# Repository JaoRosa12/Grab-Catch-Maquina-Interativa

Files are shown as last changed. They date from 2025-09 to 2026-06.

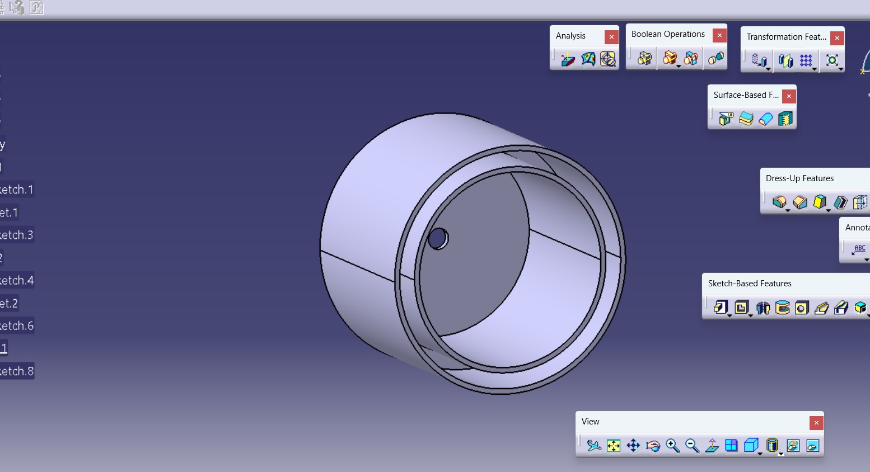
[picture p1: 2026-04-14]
DIP 06/2° Sprint/modelo 3D.jpeg

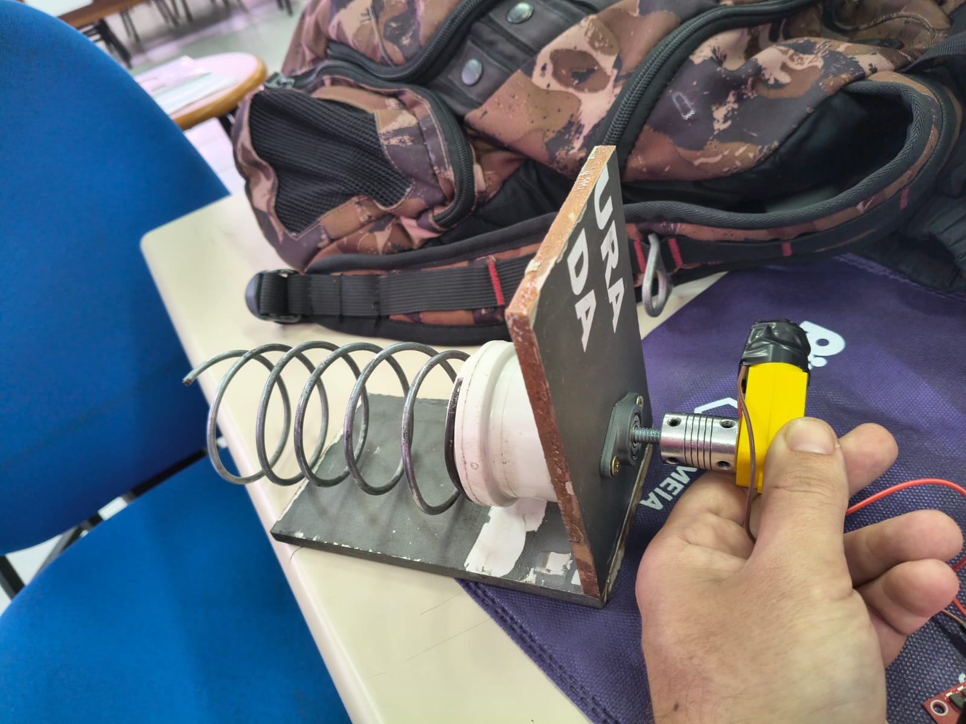
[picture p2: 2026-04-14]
DIP 06/2° Sprint/simulação mola 2.jpeg

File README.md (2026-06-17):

# Organizações Grab & Catch - Maquina Interativa

## 📌 Introdução

A Grab & Catch é uma máquina interativa desenvolvida por alunos do curso de Manufatura Avançada da Fatec São José dos Campos, no âmbito da disciplina de Desenvolvimento Integrado de Produto (DIP). A proposta é simples: o usuário enfrenta um jogo rápido na tela TFT Touch, e se vencer, ganha um brinde liberado na hora pela máquina.

O projeto integra sistemas mecânicos, eletrônicos e de programação em um único protótipo funcional, demonstrando na prática a relação entre hardware e software no processo de automação. O painel de controle é simples e acessível, com uma interface intuitiva que facilita a interação do usuário com a máquina.

## 🎯 Objetivos	

Este projeto tem como finalidade desenvolver uma máquina interativa, que proporcione praticidade e interatividade aos usuários. Para isso, será implementado um sistema de pontos e caso o usuário consiga ganhar determinados pontos, poderá escolher algum produto da máquina.

Além disso, a máquina terá um design interno que facilite tanto o armazenamento quanto a reposição contínua dos produtos. Serão também definidas normas operacionais que assegurem o uso seguro e a manutenção adequada do equipamento.

O desenvolvimento será dividido em etapas específicas, nas quais cada módulo do sistema será projetado e testado individualmente antes da integração final. A equipe contará com o apoio de orientadores para alinhar as funcionalidades às necessidades reais, promovendo ajustes contínuos ao longo do processo. O andamento será acompanhado por meio de um cronograma estruturado, que organizará as entregas e facilitará o monitoramento das atividades.

## Cronograma Macro - Entrega até a Feira de Soluções

#### Entrega 1 

| Tarefas | Colaborador | Início | Fim | 
|---|---|---|-----|
| ✅ Formalização das Equipes| João Pedro | 25/02/2026 | 25/02/2026 |
| ✅ Pesquisa dos Materias para Fabricação | João Vitor & Gabriel | 28/02/2026 | 10/03/2026 |
| ✅ Pesquisa sobre LCD TFT| João Pedro & Gabriel  |28/03/2026 | 04/03/2026 |
| ✅ Pesquisa sobre Micontroladores| João Pedro & Gabriel | 28/03/2026 | 03/03/2026 |
| ✅ Pesquisa sobre integração de iluminação da Maquina| Gabriel | 03/03/2026 | 11/03/2026 |
| ✅ Pré-Projeto Finalizado | João Vitor  | 08/03/2026 | 10/03/2026 |
| ✅ Documentação e Apresentação | Equipe | 12/03/2026 | 12/03/2026 |

#### Entrega 2

| Tarefas | Colaborador | Início | Fim | 
|---|---|---|-----|
| ✅ Pesquisa sobre a parte mecanica da mola| João Vitor & Gabriel | 15/03/2026 | 20/03/2026 |
| ✅ Pesquisa sobre a progrmação do LCD TFT| João Pedro | 16/03/2026 | 20/03/2026 |
| ✅ Desenvolvimento do Desenho Tecnico Atualizado| João Vitor | 18/03/2026| 08/04/2026 |
| ✅ Minuta do Projeto Finalizado | João Pedro | 26/03/2026 | 26/03/2026 |
| ✅ Documentação e Apresentação | Equipe | 09/04/2026 | 09/04/2026 |

#### Entrega 3

| Tarefas | Colaborador | Início | Fim | 
|---|---|---|-----|
| ✅ Montagem da Estrutura da Maquina| Equipe | 13/04/2026  |  04/05/2026  |
| ✅ Programar jogos para a Maquina | João Pedro |  15/04/2026  |  22/04/2026  |
| ✅ Visualização e testes de programação | João Pedro |  22/04/2026 |  22/04/2026  |
| ✅ Finalização do Projeto Executivo | João Pedro |  25/04/2026  | 25/04/2026  |
| ✅ Documentação e Apresentação | Equipe | 05/05/2026  | 06/05/2026  |

#### Entrega 4 

| Tarefas | Colaborador | Início | Fim | 
|---|---|---|-----|
| ✅ Montagem dos Eletrônicos  | Equipe |  09/05/2026  |  15/05/2026  |
| ✅ Sistema Mecânico na Estrutura | João Pedro |  09/05/2026  | 15/05/2026  |
| ✅ Teste de Validação | Equipe |  10/05/2026  |  16/05/2026  |  
| ✅ Ajustes Tecnicos  | Equipe  |  16/05/2026  | 18/05/2026 |
| ✅ Documentação e Apresentação | Equipe |  09/06/2026  |  11/06/2026 |

## 👥 Equipe Grab & Catch

O projeto é desenvolvido pelos seguintes integrantes:

| Nome | Foto | Área |
|---|---|---|
| **Gabriel Alves**, 📧 [Email](mailto:gabriel_alvesempresarial@hotmail.com) | Gabriel Alves | **Mecânica/Eletrônica**  |  
| **João Pedro da Silva Rosa**, 📧 [Email](mailto:joao.silvarosa16@gmail.com) | João Pedro Da Silva Rosa | **Programação/Eletrônica**  |
| **João Vitor Morais Souza**, 📧 [Email](mailto:joao.souza234@fatec.sp.gov.br) | João Vitor Morais Souza | **Mecânica/Eletrônica**  |

**Professores orientadores:**
- **Viviane Siqueira**

## 🔗 Links Úteis

- 🔗 Repositório no GitHub: [Organizações Grab & Catch - Maquina de Vendas](https://github.com/JaoRosa12/Grab-Catch-Maquina-de-Vendas)
- 🎥 Demonstração do Projeto: (*Adicionaremos o link para vídeos, se houver*)

## 📞 Contato

Caso tenha dúvidas ou sugestões, entre em contato com a equipe pelo GitHub ou através dos professores orientadores.

---

📌 **Organizações Grab & Catch - Maquina de Vendas** | Curso Superior de Tecnologia em Manufatura Avançada - Fatec - SJC

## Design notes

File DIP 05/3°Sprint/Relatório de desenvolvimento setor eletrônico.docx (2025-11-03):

Relatório de desenvolvimento setor eletrônico

Nesta etapa fizemos os testes em bancada dos componentes eletrônicos, ligando cada um deles em conjunto com o objetivo de validar seu funcionamento

Dividimos em 2 partes os testes em bancada sendo o primeiro com relação aos componentes de interação com o usuário

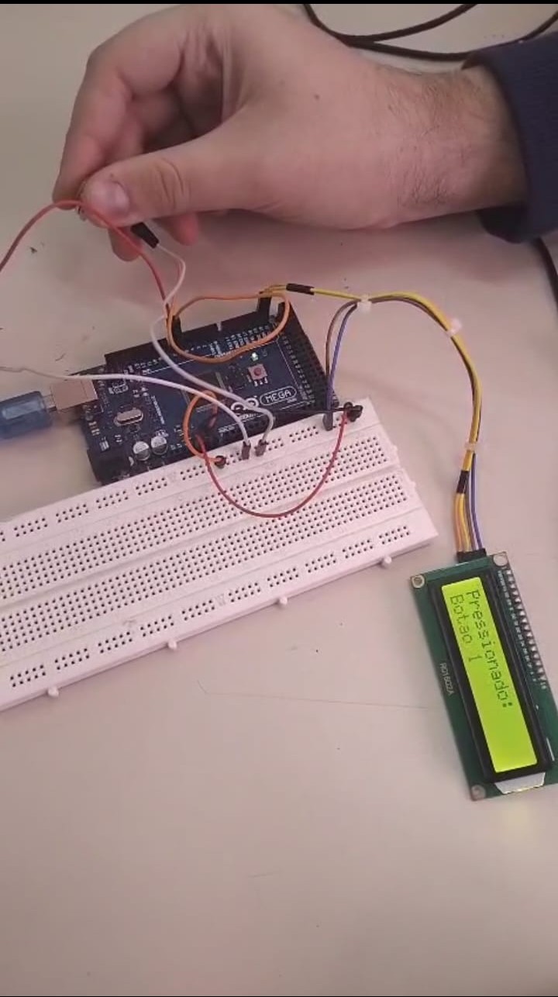
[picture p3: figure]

Componentes de teste:

- Arduino MEGA
- Display Lcd com módulo i2C
- 2 botões pushbottom

Tensão necessária para os componentes: 5V – fornecido pelo próprio Arduino

A segunda parte dos testes em bancada dessa vez foi relacionada aos componentes que irão de fato movimentar os produtos internos

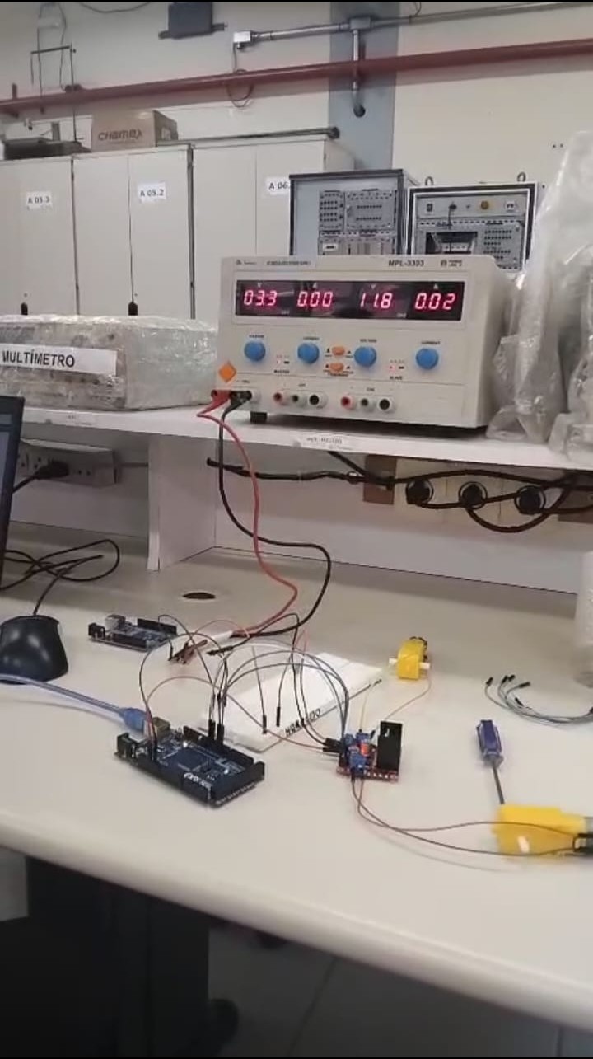
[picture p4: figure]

Componentes utilizados:

- Arduino MEGA
- Ponte H L298N
- 2 motores Dc com caixa redutora

Fonte de energia de bancada de 6V para alimentação dos motores

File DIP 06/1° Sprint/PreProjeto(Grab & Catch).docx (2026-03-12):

Curso Superior de Tecnologia em

Manufatura Avançada

projeto executivo de desenvolvimento integrado de produto VI - MÁQUINA INTERATIVA

JOÃO PEDRO DA SILVA ROSA

JOÃO VITOR MORAES DE SOUZA

GABRIEL ALVES DA SILVA

São José dos Campos

2026

RESUMO

Este pré-projeto apresenta a continuação do desenvolvimento da Máquina Interativa Grab & Catch, criada para promover a FATEC em eventos por meio de jogos interativos e distribuição de brindes. A primeira versão foi apresentada na Feira de Soluções como prova de conceito, porém apresentou limitações estruturais e mecânicas. Assim, este trabalho propõe melhorias no design, na estrutura e no sistema de funcionamento da máquina, visando tornar o protótipo mais robusto, funcional e adequado para uso em eventos institucionais.

# 1. INTRODUÇÃO

No semestre passado foi desenvolvido um projeto de uma máquina interativa que distribuía brindes para quem interagisse com seus jogos, cujo objetivo era atrair visitantes em eventos acadêmicos por meio de jogos rápidos e interativos, oferecendo brindes como recompensa pela participação do usuário. A máquina foi apresentada na Feira de Soluções da FATEC, funcionando como uma prova de conceito de um sistema interativo capaz de promover a instituição e gerar engajamento com o público.

Apesar de o projeto ter sido funcional e ter atingido seu objetivo de demonstrar o conceito da máquina interativa, alguns problemas foram observados durante o desenvolvimento e apresentação do protótipo. A estrutura construída em papel panamá apresentou baixa resistência mecânica, e o sistema de mola utilizado para a liberação dos brindes demonstrou dificuldades de funcionamento, exigindo diversos ajustes durante os testes.

Dessa forma, o presente projeto tem como proposta dar continuidade ao desenvolvimento da máquina interativa, aplicando melhorias estruturais, mecânicas e eletrônicas com base nas dificuldades identificadas no semestre anterior. A nova etapa busca tornar o protótipo mais robusto, confiável e adequado para utilização em eventos institucionais.

# 2. Justificativa

Projetos interativos são ferramentas importantes para promover instituições em eventos acadêmicos, feiras tecnológicas e atividades de divulgação científica. A utilização de sistemas automatizados capazes de oferecer experiências lúdicas ao público contribui para aumentar o interesse dos visitantes e fortalecer a imagem institucional.

Além disso, a continuação do projeto permite que os alunos aprofundem conhecimentos práticos em áreas importantes da Manufatura Avançada, como:

- Sistemas embarcados
- Integração entre eletrônica e mecânica
- Prototipagem de produtos
- Automação
- Desenvolvimento de interfaces interativas

Outro fator relevante é que o protótipo desenvolvido anteriormente apresentou limitações estruturais e mecânicas que podem ser significativamente aprimoradas nesta nova etapa do projeto. Dessa forma, a evolução da solução permitirá desenvolver um protótipo mais robusto, funcional e confiável, aproximando o projeto de um produto real.

# 3. Objetivos geral e específicos

Objetivo geral

Dar continuidade ao desenvolvimento da Máquina Interativa Grab & Catch, aplicando melhorias estruturais, mecânicas e eletrônicas para tornar o sistema mais robusto, funcional e adequado para utilização em eventos institucionais.

Objetivos específicos

Para atingir o objetivo geral deste projeto, foram definidos os seguintes objetivos específicos:

- Analisar os problemas observados no protótipo desenvolvido no semestre anterior;
- Redesenhar a estrutura física da máquina para aumentar sua resistência e estabilidade;
- Melhorar o sistema mecânico da mola responsável pela liberação dos brindes;
- Reorganizar e otimizar o sistema eletrônico baseado em Arduino;
- Substituir display LCD por um TFT Touch colorido
- Refinar o software responsável pela interface e pelos jogos interativos;

# 4. Proposta de design e funcionalidade da solução

A proposta deste projeto consiste em desenvolver uma versão aprimorada da máquina interativa Grab & Catch, mantendo o conceito original, porém com melhorias estruturais e funcionais baseadas nas dificuldades observadas anteriormente.

Estrutura desenvolvida no catia no semestre passado.

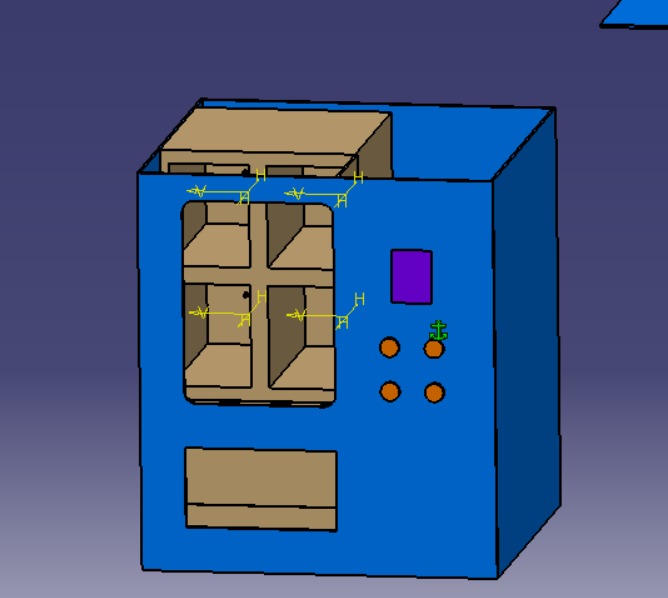
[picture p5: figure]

Fonte: Autor próprio.

Estrutura apresentada na feira de soluções no semestre passado.

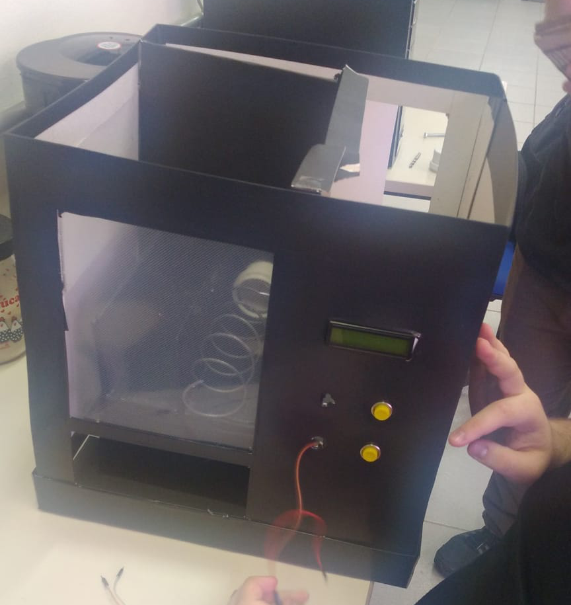
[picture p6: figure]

Fonte: Autor próprio.

# 5. Mapa Mental

Mapa mental desenvolvido.

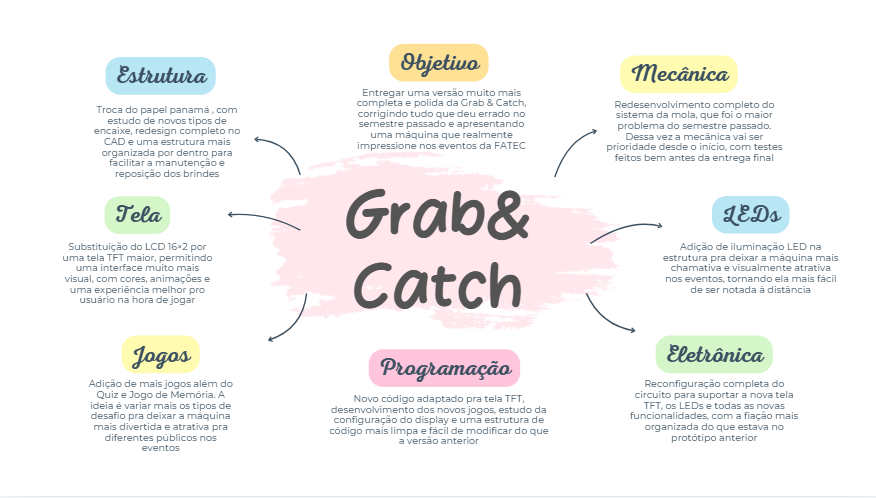
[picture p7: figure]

Fonte: Autor próprio

# 6. Lista de componentes.

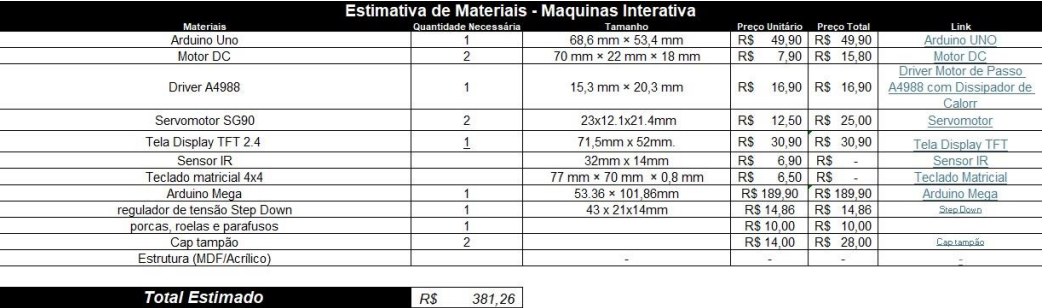
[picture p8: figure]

# 7. Cronograma Micro

Cronograma Macro desenvolvida para 1° Sprint.

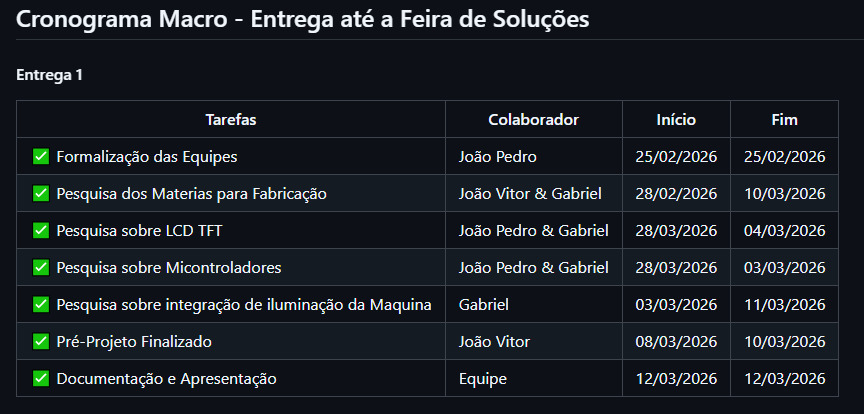
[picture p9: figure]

Fonte: Autor próprio.

# 8. REFERÊNCIAS

ARDUINO. Arduino Uno Rev3. Arduino Official Documentation, 2024. Disponível em: https://www.arduino.cc/en/Main/ArduinoBoardUno.

ARDUINO. Arduino Mega 2560 Rev3. Arduino Official Documentation, 2024. Disponível em: https://www.arduino.cc/en/Main/ArduinoBoardMega2560. Acesso em: 20 nov. 2024.

ARDUINO. LiquidCrystal Library Reference. Arduino Official Documentation, 2024. Disponível em: https://www.arduino.cc/en/Reference/LiquidCrystal

ATMEL. ATmega328P Datasheet. Atmel Corporation, 2015. Disponível em: http://www.atmel.com.

BANZI, Massimo; SHILOH, Michael. Primeiros passos com o Arduino. 2. ed. São Paulo: Novatec, 2015.

INSTRUCTABLES. Otto DIY - Build You Own Robot in Two Hours. Disponível em: https://www.instructables.com/Otto-Build-You-Own-Robot-in-Two-Hours/.

MARGOLIS, Michael. Arduino cookbook. 3. ed. Sebastopol: O'Reilly Media, 2020.

MCROBERTS, Michael. Arduino básico. São Paulo: Novatec, 2011.

MONK, Simon. Programação com Arduino: começando com sketches. 2. ed. Porto Alegre: Bookman, 2017.

TEXAS INSTRUMENTS. L293D Quadruple Half-H Driver Datasheet. Texas Instruments, 2016. Disponível em: http://www.ti.com.

Material didático do Curso Superior de Tecnologia em Manufatura Avançada. FATEC São José dos Campos, 2023-2024.

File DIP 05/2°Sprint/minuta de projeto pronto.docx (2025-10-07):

CURSO SUPERIOR DE TECNOLOGIA EM

MANUFATURA AVANÇADA

MINUTA DE PROJETO DE DESENVOLVIMENTO INTEGRADO DE PRODUTO V – MAQUINA INTERATIVA

João Pedro da Silva Rosa

João Vitor Moraes de Sousa

Gabriel Alves da Silva

# Escopo do projeto

O projeto consiste no desenvolvimento de uma máquina interativa, com o objetivo de promover a instituição FATEC. A interação presenteará aqueles que interagirem com brindes relacionados e instituição, que podem ser chaveiros, canetas, adesivos, pirulitos, bala etc. O projeto será subdividido em 3 partes principais de desenvolvimento, sendo:

- Eletrônica
- Programação
- Estrutural

O processo de desenvolvimento tem início com a montagem do circuito eletrônico do produto, que inicialmente contará com os componentes básicos para sua operação sendo:

- 2x Arduino Uno;

- 4x Motores Dc;

- 2x Driver Ponte H L298N;

- 1 Tela Display TFT 2.4 driver HX8347-D;

A partir destes componentes básicos será desenvolvido os cálculos necessários para o desenvolvimento do circuito eletrônico, relativo a suas tensões, corrente e resistências necessárias para sua aplicação

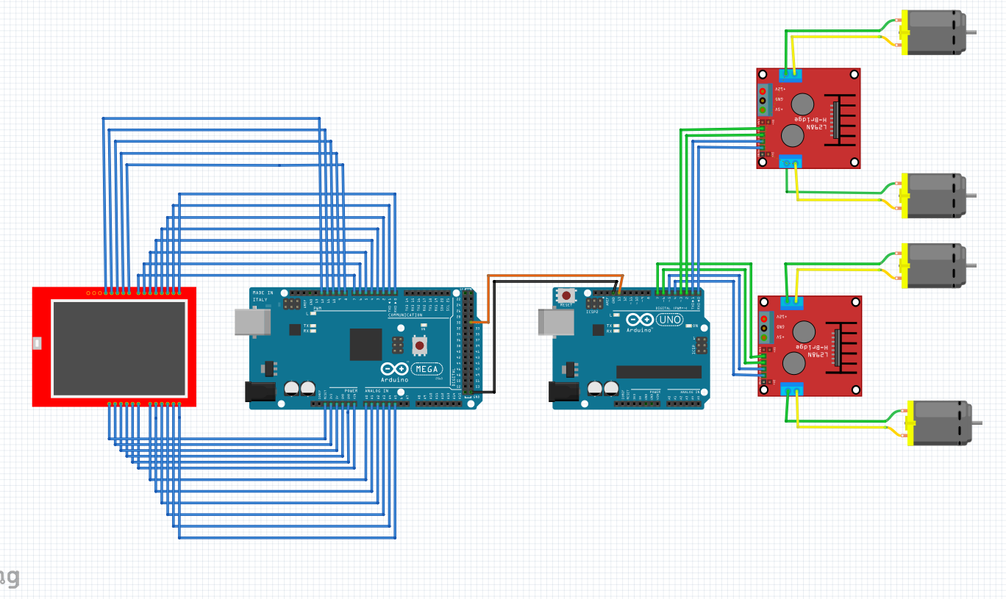
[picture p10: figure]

Fonte: autor próprio

O objetivo deste circuito primordialmente é ter uma interface de interação com o usuário (LCD) da qual com a interação do cliente se enviara um Input para os motores Dc que estarão internamente no produto, fazendo com que se acione alguma alavanca que “derrubará” o brinde ao usuário, sua recompensa pela interação.

Abaixo algumas imagens da internet retiradas como inspiração

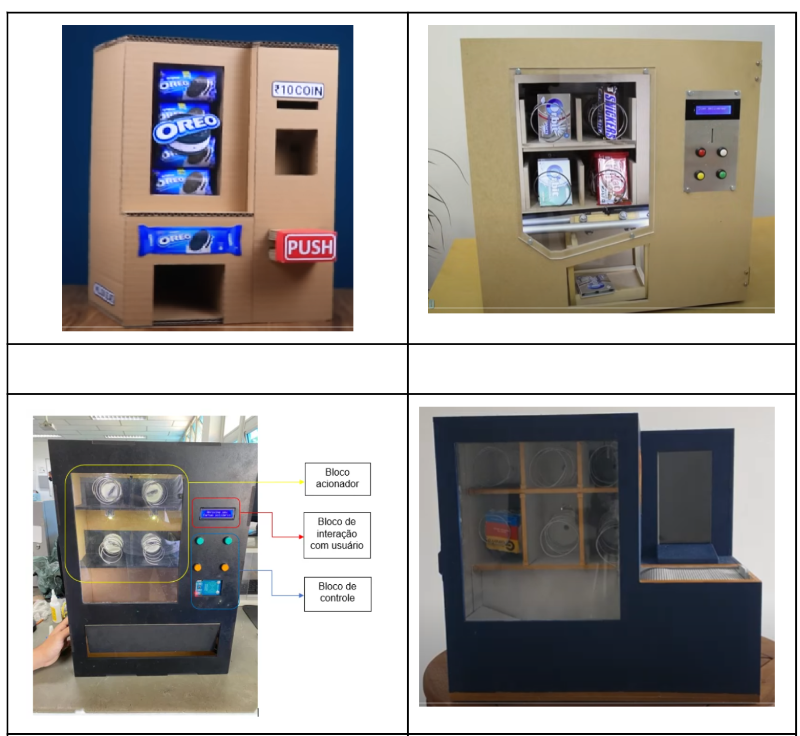
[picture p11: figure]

Fonte: imagem retiradas da internet

Croquis desenvolvidos durante a 1º Sprint

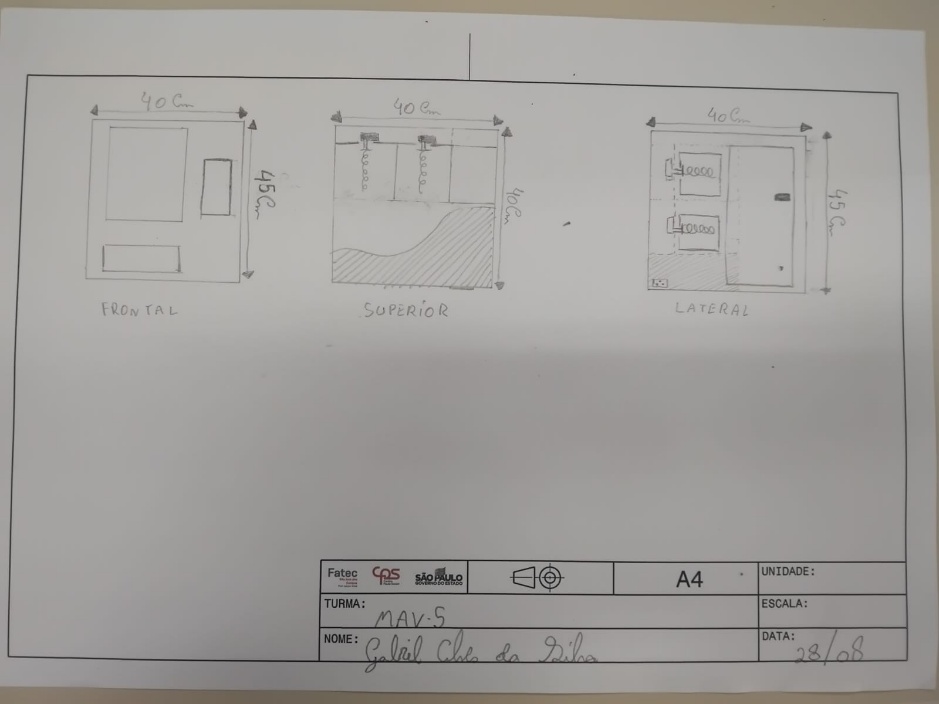
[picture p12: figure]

Fonte: Autor próprio

Estrutura desenvolvida através do software catia a partir das inspirações retiradas da internet e dos croquis desenvolvidos na 1° Sprint


Fonte: Autor próprio

# Cronograma Macro

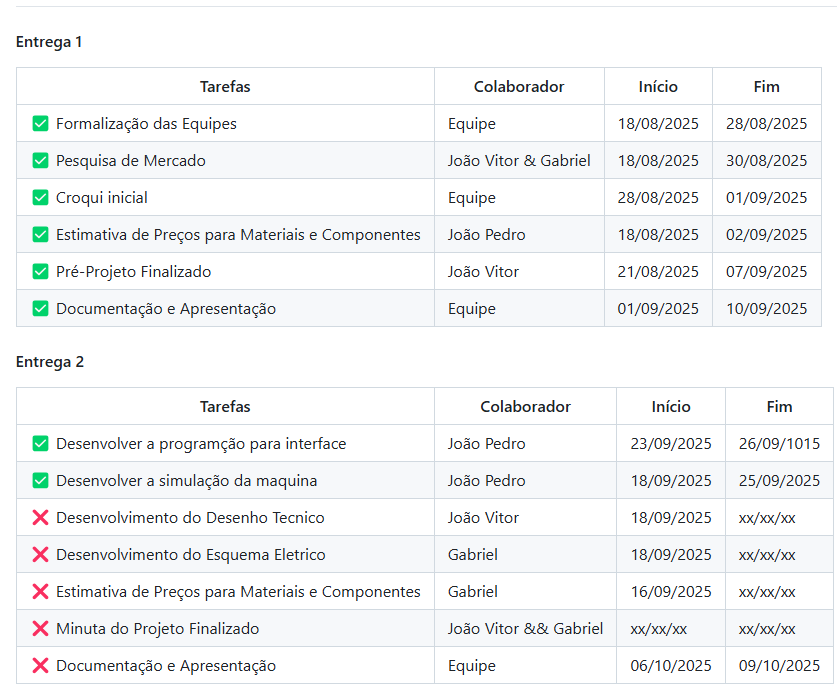
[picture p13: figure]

# Escopo do produto

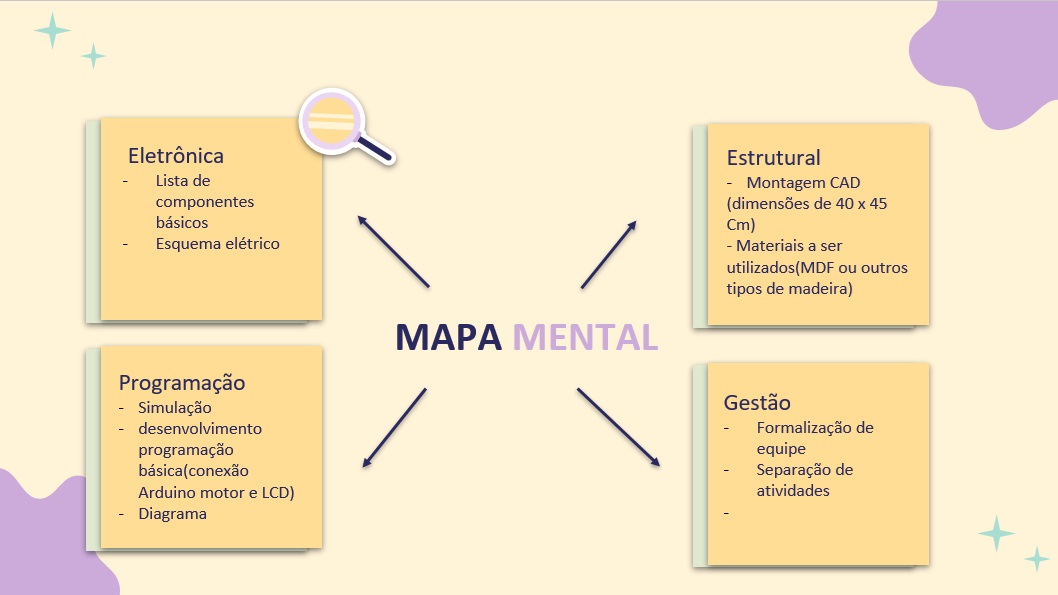
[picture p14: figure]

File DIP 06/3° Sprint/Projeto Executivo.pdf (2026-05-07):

## CURSO SUPERIOR DE TECNOLOGIA EM

## MANUFATURA AVANÇADA

## PROJETO EXECUTIVO DE DESENVOLVIMENTO

## INTEGRADO DE PRODUTO V - MÁQUINA INTERATIVA

JOÃO PEDRO DA SILVA ROSA

JOÃO VITOR MORAES DE SOUZA

GABRIEL ALVES DA SILVA

São José dos Campos

2026

2

1. 1 INTRODUÇÃO

Informações contidas na minuta do projeto. O projeto consiste no

desenvolvimento de uma máquina interativa, com o objetivo de promover a

instituição FATEC. A interação presenteará aqueles que interagirem com brindes

relacionados à instituição, que podem ser chaveiros, canetas, adesivos, pirulitos,

balas etc.

O projeto será subdividido em 3 partes principais de desenvolvimento, sendo:

Eletrônica

Programação

Estrutural

O processo de desenvolvimento tem início com a montagem do circuito

eletrônico do produto, que inicialmente contará com os componentes básicos

para sua operação sendo:

1× Arduino Uno

1× Arduino Mega

2× Motores DC

1× Driver Ponte H L293D

1× Display LCD TFT 2,4

TouchScreen

4× Botões Push Button

3

A partir destes componentes básicos foram desenvolvidos os cálculos

necessários para o desenvolvimento do circuito eletrônico, relativo a suas

tensões, corrente e resistências necessárias para sua aplicação.

O objetivo deste circuito primordialmente é ter uma interface de interação com

o usuário (LCD) da qual com a interação do cliente se enviará um Input para os

motores DC que estarão internamente no produto, fazendo com que se acione

alguma alavanca que "derrubará" o brinde ao usuário, sua recompensa pela

interação.

O sistema possui dois modos de jogo interativos: um quiz de perguntas

verdadeiro/falso, um jogo de memória de sequências, um jogo da velha e um

jogo de pong.

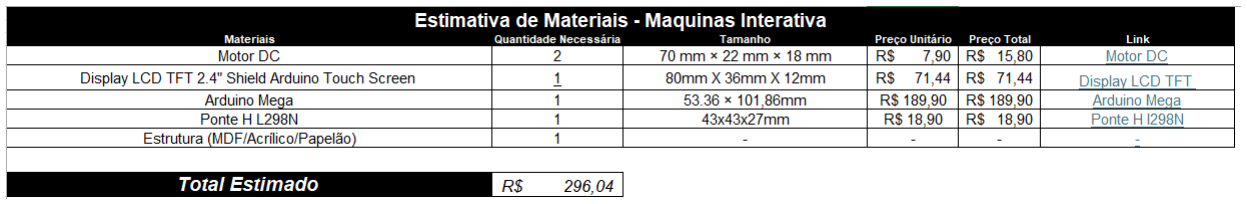
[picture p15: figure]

4

2. 2 PROJETO EXECUTIVO

O relatório do projeto executivo pode ser definido como um relatório as built –

como construído – ou como um manual D.I.Y., do it yourself – faça você mesmo

– ou ainda como um manual de instruções. Ou seja, o projeto executivo é uma

descrição de todas as etapas realizadas no decorrer do projeto onde qualquer

pessoa que tenha acesso ao relatório consiga reproduzir a solução que foi

desenvolvida.

### 2.1 Lista de Materiais e Componentes Utilizados

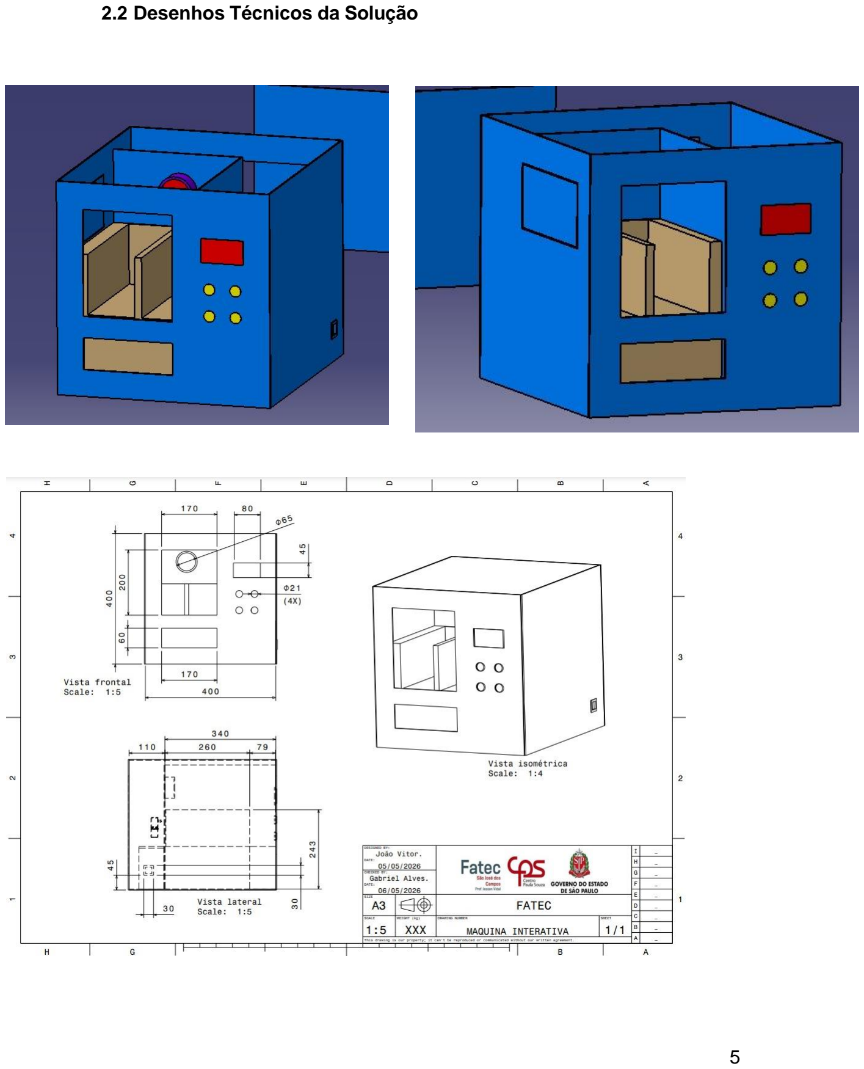
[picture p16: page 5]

5

### 2.2 Desenhos Técnicos da Solução

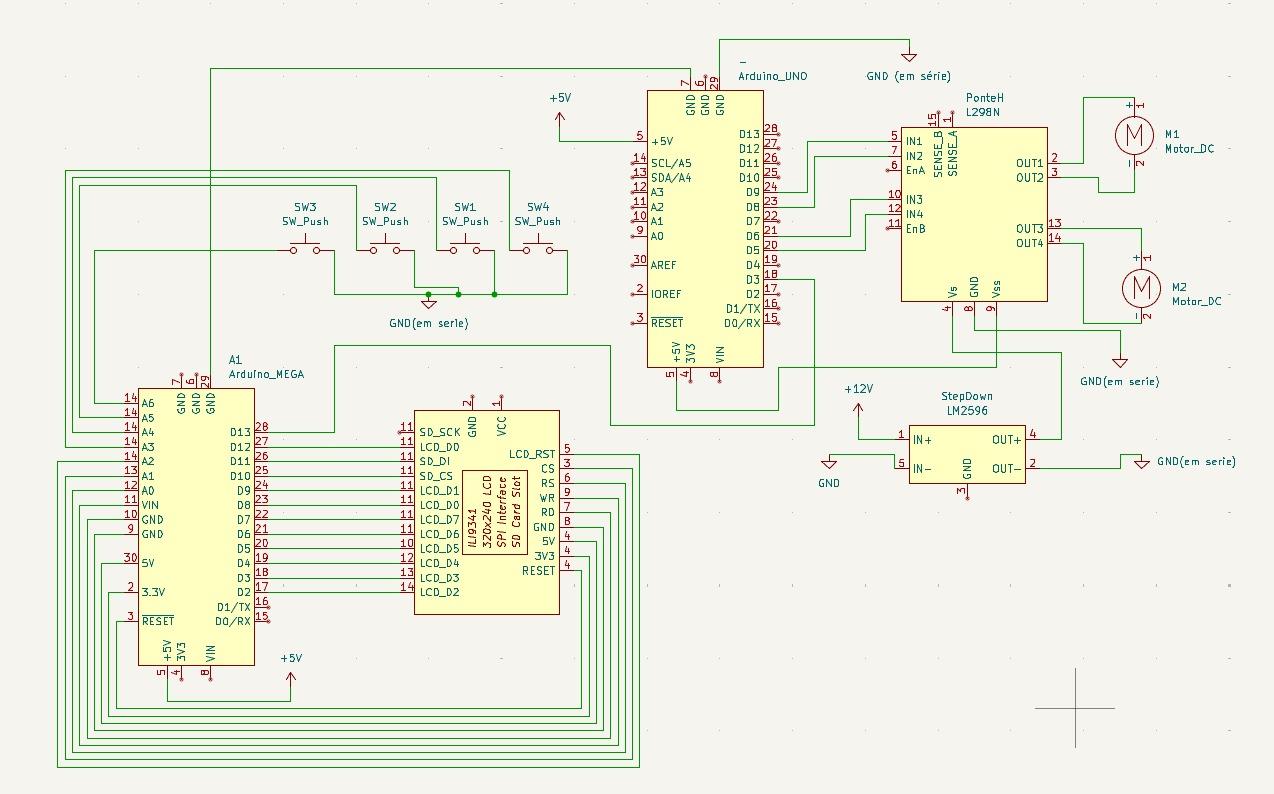
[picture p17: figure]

6

### 2.3 Circuitos Elétricos

DIAGRAMA DE BLOCOS

7

Conexões do Display TFT 2,4” (Arduino Mega — Interface)

Pino Display | Pino Arduino Mega | Função
LCD_RST | A4 | Reset do display
LCD_CS | A3 | Chip Select
LCD_RS (D/C) | A2 | Data / Command
LCD_WR | A1 | Write strobe
LCD_RD | A0 | Read strobe
LCD_D0 ~ D7 | D8 ~ D15 | Barramento de dados 8 bits
VCC | 5V | Alimentação do shield
GND | GND | Terra comum

Touch Resistivo — Pinos Avulsos (Arduino Mega — Interface)

Pino Touch | Pino Arduino Mega | Função
YP | A1 | Eixo Y positivo
XM | A2 | Eixo X negativo
YM | 7 | Eixo Y negativo
XP | 6 | Eixo X positivo

Conexões dos Botões (Arduino Interface)

Botão | Pino Arduino | Função | Resistor Pull-down
Botão A | 6 | Opção A / Pong | 10kΩ
Botão B | 7 | Opção B / Memória | 10kΩ
Botão C | 8 | Opção C / Velha | 10kΩ
Botão D | 9 | Opção D / Quiz | 10kΩ

8

Conexões dos Drivers L293D (Arduino Motor)

Pino Driver | Pino Arduino | Função
EN1 | 2 | Enable Motor 1 (PWM)
M1A | 14 (A0) | Motor 1 Input A
M1B | 15 (A1) | Motor 1 Input B
EN2 | 5 | Enable Motor 2 (PWM)
M2A | 3 | Motor 2 Input A
M2B | 4 | Motor 2 Input B
VCC1 | 5V | Lógica
VCC2 | 12V | Motores
GND | GND | Terra comum

9

Comunicação Serial entre Arduinos

Arduino Interface | Arduino Motor | Função
Serial1 — TX1 (pino 18) | SoftwareSerial — RX (pino 10) | Transmissão
GND | Serial1 — TX1 (pino 18) | Recepção
GND | GND | Terra comum

Protocolo: 9600 baud

Mensagens:

'0' = Sistema OFF (Motor → Interface)

'1' = Sistema ON (Motor → Interface)

'A' = Acionar Motor 1 (Interface → Motor)

'B' = Acionar Motor 2 (Interface → Motor)

Cálculos Elétricos —

Consumo de Corrente

de Corrente:

Arduino Mega (Interface): 80 mA (com shield TFT ativo) Arduino Uno (Motor): 50 mA (com SoftwareSerial ativo) Display TFT 2,4” ILI9341 (backlight + lógica): 60 mA
Touch resistivo: 5 mA
Botões push-button (4×, via INPUT_PULLUP interno): 2 mA
Motores DC (2× — carga nominal): 600 mA (pico de partida: até 600 mA/un.) Driver L298N (lógica interna): 36 mA
LM2596 Step-Down (eficiência ≈ 85–92%): ≈ 32 mA

Corrente total calculada (lógica + potência): ≈ 865 mA Margem de segurança (× 1,5): ≈ 1.300 mA
Pico de partida dos motores: até 1.200 mA (transitório)

Fonte especificada: 12 V — 3 A (36 W). Margem real: ≈ 2,2× sobre o consumo nominal.

10

Componentes de Proteção:

Resistores pull-down 10kΩ nos botões

Resistor 220Ω para backlight do LCD

Capacitores de desacoplamento 100nF (recomendados)

11

### 2.4 Algoritmos e Códigos

Descrição do Sistema

O software possui:

Estado OFF: Sistema aguardando ativação via interruptor

Estado MENU: Escolha entre Quiz, Jogo de Memória, Jogo

da Velha, Jogo

Estado QUIZ: 5 perguntas

Estado REFLEXO: Jogo de memória,

Estado Pong: Jogo de Pong,

Estado Jogo da Velha: Jogo de memória,

Estado FINAL: Escolha de prêmio e acionamento de motor

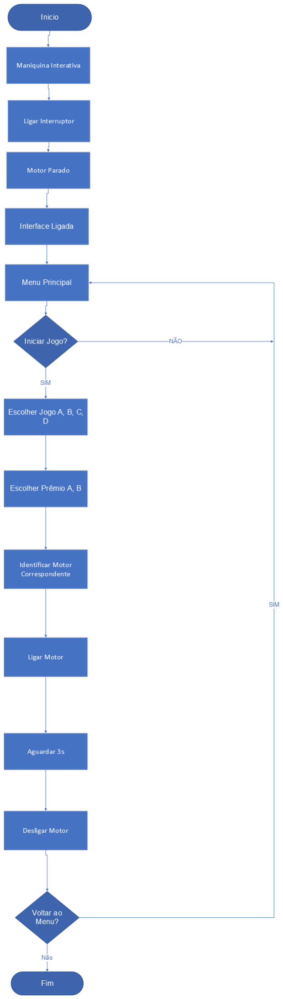
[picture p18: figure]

12

Fluxograma Principal

13

Fluxograma Motor

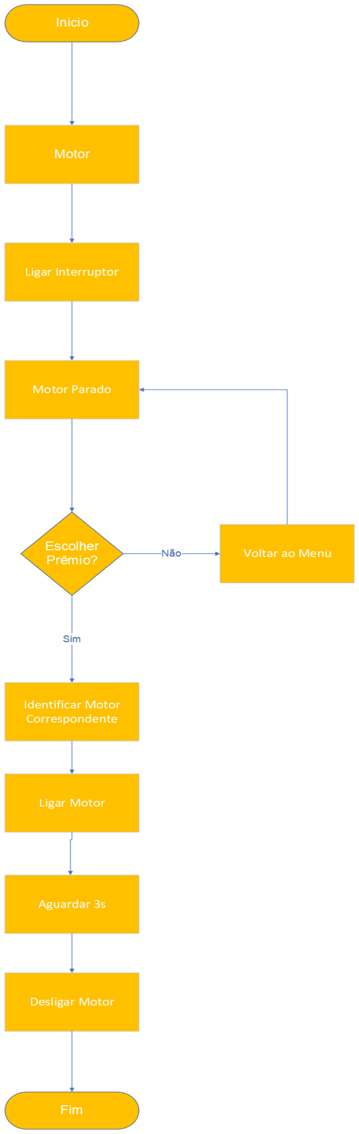
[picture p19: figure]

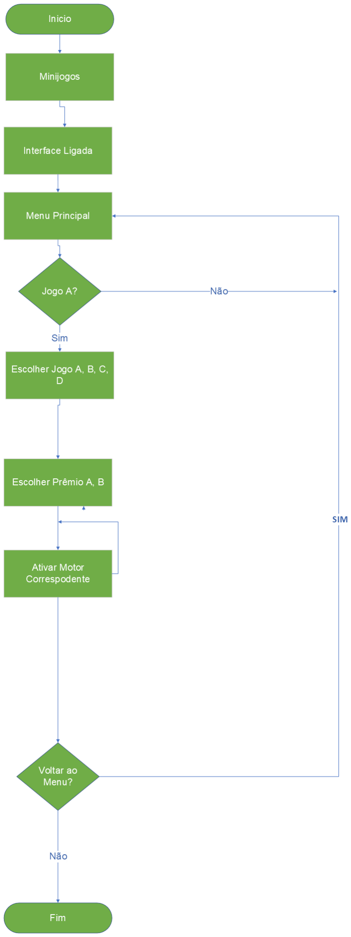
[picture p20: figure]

14

Fluxograma Interface

15

Código Arduino Interface

#include <MCUFRIEND_kbv.h> #include "graphics.h"

#include "touch.h"

#include "buttons.h"

#include "menu.h"

#include "pong.h"

#include "velha.h"

#include "quiz.h"

#include "memoria.h"

//
─────────────────────────────────────────────────────────── ──────────────────
// DISPLAY — instância global compartilhada via extern nos módulos
//
─────────────────────────────────────────────────────────── ──────────────────
MCUFRIEND_kbv tft;

//
─────────────────────────────────────────────────────────── ──────────────────
// MÁQUINA DE ESTADOS
//
─────────────────────────────────────────────────────────── ──────────────────
enum GameState {
STATE_MENU,
STATE_PONG,
STATE_VELHA,
STATE_QUIZ,
STATE_MEMORIA,
STATE_MOTOR_SELECT // ← tela de escolha de motor após vitória };
static GameState currentState = STATE_MENU;

//
─────────────────────────────────────────────────────────── ──────────────────
// TELA DE SELEÇÃO DE MOTOR
// Layout: título centralizado + dois botões lado a lado
// [ PIRULITO ] [ BALA ]
//
───────────────────────────────────────────────────────────

16

──────────────────
#define MBTN_W 130

#define MBTN_H 64

#define MBTN_Y 130

#define MBTN_AX 10

#define MBTN_BX 180

static void drawMotorSelectScreen() { tft.fillScreen(BLACK);
drawStarfield();

// Título
tft.setTextSize(2);
tft.setTextColor(NEON_YELLOW); tft.setCursor(30, 20);
tft.print(F("VOCE VENCEU!"));

tft.setTextSize(1);
tft.setTextColor(WHITE);
tft.setCursor(52, 50);
tft.print(F("Escolha seu premio:"));

tft.setTextSize(1);
tft.setTextColor(MIDGRAY); tft.setCursor(30, 70);
tft.print(F("Qual motor deseja girar?"));

// Botao Motor A
drawNeonRect(MBTN_AX, MBTN_Y, MBTN_W, MBTN_H, NEON_CYAN, 6); tft.setTextSize(2);
tft.setTextColor(NEON_CYAN);
tft.setCursor(MBTN_AX + 22, MBTN_Y + 12);
tft.print(F("PIRU-"));
tft.setCursor(MBTN_AX + 10, MBTN_Y + 36);
tft.print(F("LITO"));

// Botao Motor B
drawNeonRect(MBTN_BX, MBTN_Y, MBTN_W, MBTN_H, NEON_PINK, 6); tft.setTextSize(2);
tft.setTextColor(NEON_PINK);
tft.setCursor(MBTN_BX + 22, MBTN_Y + 12);
tft.print(F("BALA"));
}

// Retorna 'A', 'B', ou 0 se não tocou em nenhum botão
static char motorSelectCheck(int tx, int ty) {
// O eixo X e mapeado invertido no touch (SCREEN_W->0), entao
// desinverte para comparar com as coordenadas de desenho dos botoes.

17

int txM = SCREEN_W - tx;
if (ty >= MBTN_Y && ty <= MBTN_Y + MBTN_H) {
if (txM >= MBTN_AX && txM <= MBTN_AX + MBTN_W) return 'A'; if (txM >= MBTN_BX && txM <= MBTN_BX + MBTN_W) return 'B'; }
return 0;
}

//
─────────────────────────────────────────────────────────── ──────────────────
// TRANSIÇÃO PARA SELEÇÃO DE MOTOR (chamada quando jogo termina com vitória) //
─────────────────────────────────────────────────────────── ──────────────────
static unsigned long motorSelectEnterTime = 0;
#define MOTOR_SELECT_GUARD_MS 400

static void enterMotorSelect() {
currentState = STATE_MOTOR_SELECT; motorSelectEnterTime = millis(); drawMotorSelectScreen();
}

//
─────────────────────────────────────────────────────────── ──────────────────
// SETUP
//
─────────────────────────────────────────────────────────── ──────────────────
void setup() {
Serial1.begin(9600); // TX1 (pino 18) → Arduino Uno RX (pino 10)
buttonsInit(); // 4 botões físicos (pinos 22-25)

uint16_t id = tft.readID();
tft.begin(id);
tft.setRotation(1);
tft.fillScreen(BLACK);

touchLoadCalib();

// Segurar o touch no boot → entra na calibração {
TSPoint p = ts.getPoint();
pinMode(YP, OUTPUT); pinMode(XM, OUTPUT); digitalWrite(YP, HIGH); digitalWrite(XM, HIGH);
if (p.z >= MINPRESSURE && p.z <= MAXPRESSURE) {

18

touchRunCalibration();
}
}

drawMenu();
}

//
─────────────────────────────────────────────────────────── ──────────────────
// LOOP
//
─────────────────────────────────────────────────────────── ──────────────────
void loop() {
// Uma única leitura do hardware por frame — atualiza todas as flags
touchUpdate();
buttonsUpdate(); // lê os 4 botões físicos

unsigned long now = millis();

switch (currentState) {

// ── MENU
─────────────────────────────────────────────────────────── ─────
case STATE_MENU:
// Touch na tela
if (touchJustPressed()) {
int btn = checkMenuTouch(touchX(), touchY());
if (btn == 1) { currentState = STATE_PONG; pongInit(); } if (btn == 2) { currentState = STATE_VELHA; velhaFullReset(); }
if (btn == 3) { currentState = STATE_QUIZ; quizInit(); | }
if (btn == 4) { currentState = STATE_MEMORIA; memInit(); | }
}
// Botões físicos: BTN1=Pong, BTN2=Velha, BTN3=Quiz, BTN4=Memória
if (btnJustPressed(1)) { currentState = STATE_PONG; | pongInit(); | }
if (btnJustPressed(2)) { currentState = STATE_VELHA; velhaFullReset(); }
if (btnJustPressed(3)) { currentState = STATE_QUIZ; quizInit(); | }
if (btnJustPressed(4)) { currentState = STATE_MEMORIA; memInit(); | }
break;

// ── PONG
─────────────────────────────────────────────────────────── ─────
case STATE_PONG:
pongLoop(now);
if (pongIsDone()) {

19

if (pongPlayerWon()) { enterMotorSelect(); }
else { currentState = STATE_MENU; drawMenu(); } }
break;

// ── VELHA
─────────────────────────────────────────────────────────── ────
case STATE_VELHA:
velhaLoop(now);
if (velhaIsDone()) {
if (velhaPlayerWon()) { enterMotorSelect(); }
else { currentState = STATE_MENU; drawMenu(); } }
break;

// ── QUIZ
─────────────────────────────────────────────────────────── ─────
case STATE_QUIZ:
quizLoop(now);
if (quizIsDone()) {
if (quizPlayerWon()) { enterMotorSelect(); }
else { currentState = STATE_MENU; drawMenu(); } }
break;

// ── MEMÓRIA
─────────────────────────────────────────────────────────── ──
case STATE_MEMORIA:
memLoop(now);
if (memIsDone()) {
if (memPlayerWon()) { enterMotorSelect(); }
else { currentState = STATE_MENU; drawMenu(); } }
break;

// ── SELEÇÃO DE MOTOR
──────────────────────────────────────────────────── case STATE_MOTOR_SELECT:
if (touchJustPressed() && (millis() - motorSelectEnterTime >= MOTOR_SELECT_GUARD_MS)) {
char choice = motorSelectCheck(touchX(), touchY());
if (choice == 'A' || choice == 'B') {
Serial1.write(choice); // envia 'A' ou 'B' para o Uno Serial1.flush();
currentState = STATE_MENU;

20

drawMenu();
}
}
break;
}
}

21

Código Arduino Motor

#include <SoftwareSerial.h>

// --- Serial ------------------------------------------------------------------
#define RX_PIN 10 // recebe do Mega TX1 (pino 18)

#define TX_PIN 11 // nao usado, mas SoftwareSerial exige declarar SoftwareSerial megaSerial(RX_PIN, TX_PIN);

// --- Pinos motor -------------------------------------------------------------#define IN1 7 // Motor A direcao +
#define IN2 8 // Motor A direcao -

#define IN3 4 // Motor B direcao +

#define IN4 5 // Motor B direcao -

#define MOTOR_RUN_MS 9000UL // tempo de giro: 9 segundos

static bool | motorRodando = false;
static char | motorAtivo = 0;
static unsigned long motorInicio = 0;

// --- Funcoes de controle -----------------------------------------------------void ligarMotorA() {
digitalWrite(IN1, LOW);
digitalWrite(IN2, HIGH);
}

void ligarMotorB() {
digitalWrite(IN3, LOW);
digitalWrite(IN4, HIGH);
}

void pararMotores() {
digitalWrite(IN1, LOW);
digitalWrite(IN2, LOW);
digitalWrite(IN3, LOW);
digitalWrite(IN4, LOW);
}

// --- Setup -------------------------------------------------------------------void setup() {
megaSerial.begin(9600);

pinMode(IN1, OUTPUT); pinMode(IN2, OUTPUT);
pinMode(IN3, OUTPUT); pinMode(IN4, OUTPUT); pararMotores();

// Pisca Motor A 400ms no boot para confirmar que hardware esta OK

22

// Se o motor nao pulsou aqui -> verificar jumpers ENA/ENB e alimentacao ligarMotorA(); delay(400); pararMotores();
}

// --- Loop --------------------------------------------------------------------
void loop() {
unsigned long agora = millis();

if (megaSerial.available()) {
char cmd = megaSerial.read();

if (cmd == 'A') {
pararMotores();
motorAtivo = 'A'; motorInicio = agora; motorRodando = true; ligarMotorA();
}
else if (cmd == 'B') {
pararMotores();
motorAtivo = 'B'; motorInicio = agora; motorRodando = true; ligarMotorB();
}
// 'W' ignorado
}

// Para o motor apos MOTOR_RUN_MS milissegundos
if (motorRodando && (agora - motorInicio >= MOTOR_RUN_MS)) { pararMotores();
motorRodando = false;
motorAtivo = 0;
}
}

23

### 2.5 Manual de Operação Básico

Para Ligar o Sistema:

Conectar fonte à tomada

Acionar interruptor

Sistema entra no Menu Principal automaticamente

Para Jogar Quiz:

No menu, pressionar o jogo de Quiz

Ler pergunta no Display TFT

Selecionar a resposta correta

Ao final das perguntas, escolher a opção entre “Pirulito” ou “Balas”

Para Jogar Memória:

No menu, pressionar o Jogo da Memoria

Observar sequência mostrada

Repetir sequência pressionando botões

Ao final das partida, escolher a opção entre “Pirulito”

ou “Balas”

Para Jogar Jogo da Velha:

No menu, pressionar o Jogo da Velha

Observar posições mostrada

Ao final das partida, escolher a

opção entre “Pirulito” ou “Balas”

Para Jogar Pong:

No menu, pressionar o jogo de Pong

Observar a movimentação da bola

Ao final das perguntas, escolher a opção entre

“Pirulito” ou “Balas”

24

Para Receber Prêmio:

Na tela final da partida, pressionar botão do prêmio desejado

Aguardar 3 segundos (motor acionando)

Retirar brinde da bandeja inferior

Após pressionar a opção desejada voltar ao menu ou desligar

Para Desligar:

Desligar interruptor

Display apaga

Sistema desliga

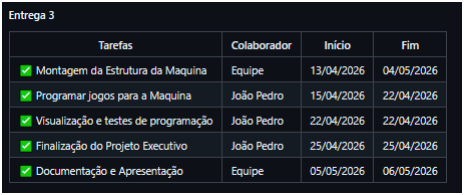
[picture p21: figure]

25

### 2.6 CRONOGRAMA MACRO

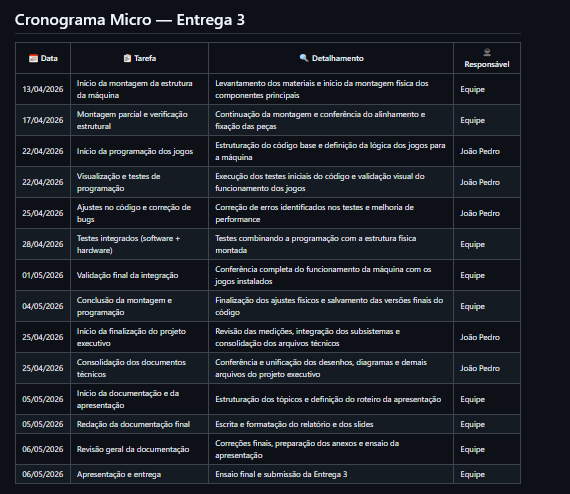
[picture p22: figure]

26

### 2.7 CRONOGRAMA MICRO

27

### 3 REFERÊNCIAS

ARDUINO. Arduino Uno Rev3. Arduino Official Documentation, 2024.

Disponível em: https://www.arduino.cc/en/Main/ArduinoBoardUno.

ARDUINO. LiquidCrystal Library Reference. Arduino Official

Documentation, 2024. Disponível em:

https://www.arduino.cc/en/Reference/LiquidCrystal

ATMEL. ATmega328P Datasheet. Atmel Corporation, 2015. Disponível em:

http://www.atmel.com.

BANZI, Massimo; SHILOH, Michael. Primeiros passos com o Arduino. 2.

ed. São Paulo: Novatec, 2015.

INSTRUCTABLES. Otto DIY - Build You Own Robot in Two Hours.

Disponível em: https://www.instructables.com/Otto-Build-You-Own-Robot-in-

Two-Hours/. (https://www.instructables.com/Otto-Build-You-Own-Robot-in-Two-Hours/)

MARGOLIS, Michael. Arduino cookbook. 3. ed. Sebastopol: O'Reilly

Media, 2020.

MCROBERTS, Michael. Arduino básico. São Paulo: Novatec, 2011.

MONK, Simon. Programação com Arduino: começando com sketches.

2. ed. Porto Alegre: Bookman, 2017.

TEXAS INSTRUMENTS. L293D Quadruple Half-H Driver Datasheet.

Texas Instruments, 2016. Disponível em: http://www.ti.com.

Material didático do Curso Superior de Tecnologia em Manufatura

Avançada. FATEC São José dos Campos, 2023-2024.

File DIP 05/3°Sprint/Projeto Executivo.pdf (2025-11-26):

## CURSO SUPERIOR DE TECNOLOGIA EM

## MANUFATURA AVANÇADA

## PROJETO EXECUTIVO DE DESENVOLVIMENTO

## INTEGRADO DE PRODUTO V - MÁQUINA INTERATIVA

JOÃO PEDRO DA SILVA ROSA

JOÃO VITOR MORAES DE SOUZA

GABRIEL ALVES DA SILVA

São José dos Campos

2025

2

1. 1 INTRODUÇÃO

Informações contidas na minuta do projeto. O projeto consiste no

desenvolvimento de uma máquina interativa, com o objetivo de promover a

instituição FATEC. A interação presenteará aqueles que interagirem com brindes

relacionados à instituição, que podem ser chaveiros, canetas, adesivos, pirulitos,

balas etc.

O projeto será subdividido em 3 partes principais de desenvolvimento, sendo:

Eletrônica

Programação

Estrutural

O processo de desenvolvimento tem início com a montagem do circuito

eletrônico do produto, que inicialmente contará com os componentes básicos

para sua operação sendo:

1× Arduino Uno

1× Arduino Mega

4× Motores DC

2× Driver Ponte H L293D

1× Display LCD 16×2

4× Botões Push Button

1× Interruptor

3

A partir destes componentes básicos foram desenvolvidos os cálculos

necessários para o desenvolvimento do circuito eletrônico, relativo a suas

tensões, corrente e resistências necessárias para sua aplicação.

O objetivo deste circuito primordialmente é ter uma interface de interação com

o usuário (LCD) da qual com a interação do cliente se enviará um Input para os

motores DC que estarão internamente no produto, fazendo com que se acione

alguma alavanca que "derrubará" o brinde ao usuário, sua recompensa pela

interação.

O sistema possui dois modos de jogo interativos: um quiz de perguntas

verdadeiro/falso e um jogo de memória de sequências. O usuário acumula

pontos e ao final escolhe um prêmio (A, B, C ou D) que é dispensado

automaticamente.

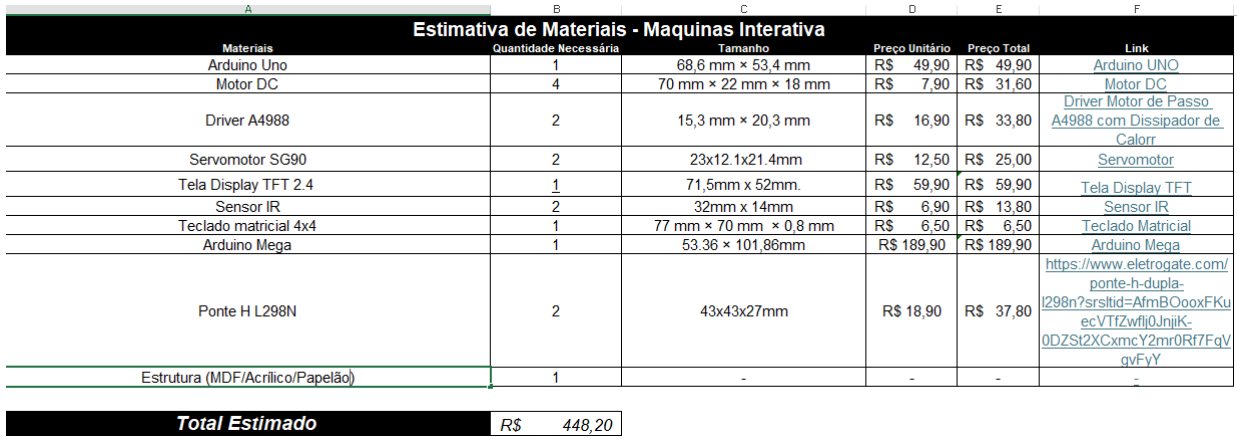
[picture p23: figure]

4

2. 2 PROJETO EXECUTIVO

O relatório do projeto executivo pode ser definido como um relatório as built –

como construído – ou como um manual D.I.Y., do it yourself – faça você mesmo

– ou ainda como um manual de instruções. Ou seja, o projeto executivo é uma

descrição de todas as etapas realizadas no decorrer do projeto onde qualquer

pessoa que tenha acesso ao relatório consiga reproduzir a solução que foi

desenvolvida.

### 2.1 Lista de Materiais e Componentes Utilizados

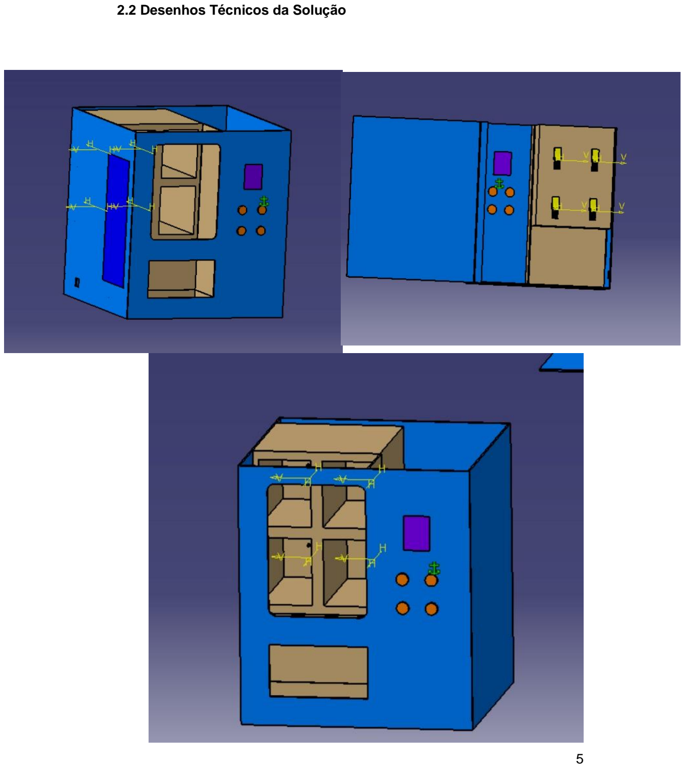
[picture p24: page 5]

5

### 2.2 Desenhos Técnicos da Solução

6

### 2.3 Circuitos Elétricos

DIAGRAMA DE BLOCOS

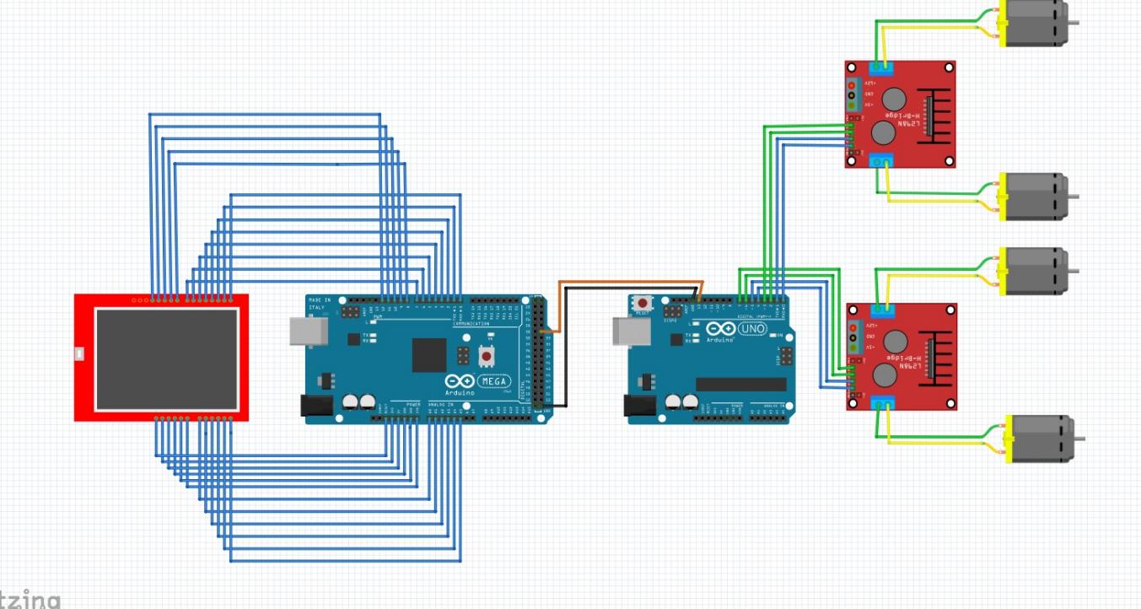
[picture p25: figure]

7

Conexões do Display LCD 16×2 (Arduino Interface)

Pino Display | Pino Arduino | Função
VSS | GND | Terra
VDD | 5V | Alimentação
V0 | Potenciômetro | Contraste
RS | 12 | Register Select
RW | GND | Read/Write (Write)
E | 11 | Enable
D4 | 5 | Data Bit 4
D5 | 4 | Data Bit 5
D6 | 3 | Data Bit 6
D7 | 2 | Data Bit 7
A | 5V (+ resistor 220Ω) | Backlight +
K | GND | Backlight -

Conexões dos Botões (Arduino Interface)

Botão | Pino Arduino | Função | Resistor Pull-down
Botão A | 6 | Quiz V / Menu | 10kΩ
Botão B | 7 | Quiz F / Memória | 10kΩ
Botão C | 8 | Próxima / Final | 10kΩ
Botão D | 9 | Opção D | 10kΩ

Conexões dos Drivers L293D (Arduino Motor)

Pino Driver | Pino Arduino | Função
EN1 | 2 | Enable Motor 1 (PWM)
M1A | 14 (A0) | Motor 1 Input A
M1B | 15 (A1) | Motor 1 Input B
EN2 | 5 | Enable Motor 2 (PWM)
M2A | 3 | Motor 2 Input A
M2B | 4 | Motor 2 Input B
VCC1 | 5V | Lógica
VCC2 | 12V | Motores
GND | GND | Terra comum

8

Interruptor

Componente | Pino Arduino Motor | Configuração
Switch | 6 | INPUT_PULLUP

Comunicação Serial entre Arduinos

Arduino Interface | Arduino Motor | Função
TX (1) | RX (0) | Transmissão
RX (0) | TX (1) | Recepção
GND | GND | Terra comum

Protocolo: 9600 baud

Mensagens:

'0' = Sistema OFF (Motor → Interface)

'1' = Sistema ON (Motor → Interface)

'A' = Acionar Motor 1 (Interface → Motor)

'B' = Acionar Motor 2 (Interface → Motor)

'C' = Acionar Motor 3 (Interface → Motor)

'D' = Acionar Motor 4 (Interface → Motor)

Cálculos Elétricos

Consumo de Corrente:

Arduinos: 2 × 50mA = 100mA

Display LCD: 20mA

Motores DC: 4 × 200mA = 800mA (máximo)

Drivers: 2 × 50mA = 100mA

Total máximo: 1020mA + margem 100% = ~2A

Fonte especificada: 12V, 3A

Componentes de Proteção:

Resistores pull-down 10kΩ nos botões

Resistor 220Ω para backlight do LCD

Capacitores de desacoplamento 100nF (recomendados)

9

### 2.4 Algoritmos e Códigos

Descrição do Sistema

O software possui:

Estado OFF: Sistema aguardando ativação via interruptor

Estado MENU: Escolha entre Quiz ou Jogo de Memória

Estado QUIZ: 10 perguntas V/F, +10 pontos por acerto

Estado REFLEXO: Jogo de memória, 5 níveis, +10×N pontos

Estado FINAL: Escolha de prêmio e acionamento de motor

10

Fluxograma Principal

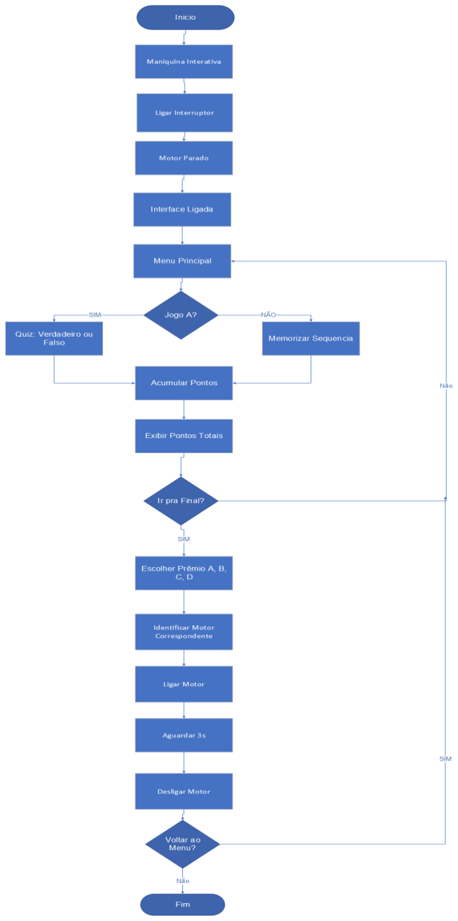
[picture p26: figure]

11

Fluxograma Motor


12

Fluxograma Interface


13

Código Arduino Interface

#include <LiquidCrystal.h>

LiquidCrystal lcd(12, 11, 5, 4, 3, 2);

// Pinos

const byte BTN[4] = {6, 7, 8, 9}; // A, B, C, D

// Estados

enum Estado : byte { OFF, MENU, QUIZ, REFLEXO, FINAL };

Estado estado = OFF;

bool ligado = false;

// Variáveis globais

int pontos = 0;

byte idx = 0;

bool flag = false;

// Quiz - armazenado em PROGMEM (Flash) para economizar RAM

const char q0[] PROGMEM = "O Brasil tem 5";

const char q1[] PROGMEM = "regioes?";

const char q2[] PROGMEM = "A agua ferve a";

const char q3[] PROGMEM = "100 graus C?";

const char q4[] PROGMEM = "O Sol e uma";

const char q5[] PROGMEM = "estrela?";

const char q6[] PROGMEM = "Existem 12";

const char q7[] PROGMEM = "meses no ano?";

const char q8[] PROGMEM = "A Terra e";

const char q9[] PROGMEM = "plana?";

const char q10[] PROGMEM = "Os peixes";

14

const char q11[] PROGMEM = "respiram agua?";

const char q12[] PROGMEM = "O gelo e mais";

const char q13[] PROGMEM = "pesado q agua?";

const char q14[] PROGMEM = "Ha 60 minutos";

const char q15[] PROGMEM = "em 1 hora?";

const char q16[] PROGMEM = "Os morcegos";

const char q17[] PROGMEM = "sao cegos?";

const char q18[] PROGMEM = "A velocidade da";

const char q19[] PROGMEM = "luz e constante?";

const char* const perguntas[] PROGMEM = {

q0, q1, q2, q3, q4, q5, q6, q7, q8, q9,

q10, q11, q12, q13, q14, q15, q16, q17, q18, q19

};

const bool respostas[] PROGMEM = {1,1,1,1,0,0,0,1,0,1};

// Reflexo/Memória

byte seq[10], pos, nivel, ptsTemp;

bool mostrando, esperando, fim;

char buffer[17];

void setup() {

lcd.begin(16, 2);

for(byte i=0; i<4; i++) pinMode(BTN[i], INPUT);

Serial.begin(9600);

randomSeed(analogRead(A0));

delay(2000);

lcd.noDisplay();

}

void loop() {

if (Serial.available()) {

15

char c = Serial.read();

if (c == '1' && !ligado) ligar();

else if (c == '0' && ligado) desligar();

}

if (ligado) {

switch(estado) {

case MENU: loopMenu(); break;

case QUIZ: loopQuiz(); break;

case REFLEXO: loopReflexo(); break;

case FINAL: loopFinal(); break;

}

}

delay(50);

}

void ligar() {

ligado = true;

lcd.display();

lcd.clear();

lcd.print(F("SISTEMA LIGADO!"));

delay(1500);

pontos = 0;

menu();

}

void desligar() {

ligado = false;

estado = OFF;

pontos = 0;

lcd.clear();

lcd.noDisplay();

}

16

void menu() {

estado = MENU;

lcd.clear();

lcd.print(F("ESCOLHA O JOGO:"));

lcd.setCursor(0, 1);

lcd.print(F("A=Quiz B=Reflexo")); }

void loopMenu() {

if (lerBtn(0)) initQuiz();

if (lerBtn(1)) initReflexo(); }

// ===== QUIZ =====

void initQuiz() {

estado = QUIZ;

idx = 0;

ptsTemp = 0;

flag = false;

fim = false;

lcd.clear();

lcd.print(F("INICIANDO QUIZ"));

delay(1000);

mostrarQ(); }

void mostrarQ() {

lcd.clear();

lcd.print(F("Q"));

lcd.print(idx + 1);

lcd.print(F("/10:"));

lcd.setCursor(0, 1);

17

strcpy_P(buffer, (char*)pgm_read_word(&(perguntas[idx*2])));

lcd.print(buffer);

delay(1500);

lcd.clear();

strcpy_P(buffer, (char*)pgm_read_word(&(perguntas[idx*2+1])));

lcd.print(buffer);

lcd.setCursor(0, 1);

lcd.print(F("A=V B=F"));

flag = false;

}

void loopQuiz() {

if (Serial.available() && Serial.read() == '0') {

desligar();

return;

}

if (!fim) {

if (!flag && lerBtn(0)) verificarResp(true);

if (!flag && lerBtn(1)) verificarResp(false);

if (flag && lerBtn(2)) proxQ();

}

}

void verificarResp(bool r) {

flag = true;

lcd.clear();

if (r == pgm_read_byte(&respostas[idx])) {

ptsTemp += 10;

lcd.print(F("CORRETO! +10pts"));

18

} else {

lcd.print(F("ERRADO!"));

lcd.setCursor(0, 1);

lcd.print(F("Resp: "));

lcd.print(pgm_read_byte(&respostas[idx]) ? 'V' : 'F');

}

delay(1500);

lcd.clear();

lcd.print(F("Pontos: "));

lcd.print(ptsTemp);

lcd.setCursor(0, 1);

lcd.print(F("C = Proxima"));

}

void proxQ() {

if (++idx >= 10) finQuiz();

else mostrarQ();

}

void finQuiz() {

fim = true;

pontos += ptsTemp;

lcd.clear();

lcd.print(F("Quiz Completo!"));

lcd.setCursor(0, 1);

lcd.print(F("Pontos: "));

lcd.print(ptsTemp);

delay(2000);

pergProx();

}

// ===== REFLEXO/MEMÓRIA =====

19

void initReflexo() {

estado = REFLEXO;

nivel = 1;

ptsTemp = 0;

fim = false;

lcd.clear();

lcd.print(F("JOGO DE MEMORIA"));

lcd.setCursor(0, 1);

lcd.print(F("Decorar sequenc"));

delay(2000);

initNivel();

}

void initNivel() {

for(byte i=0; i<nivel; i++) seq[i] = random(1, 5);

mostrarSeq();

}

void mostrarSeq() {

mostrando = true;

lcd.clear();

lcd.print(F("NIVEL "));

lcd.print(nivel);

lcd.setCursor(0, 1);

lcd.print(F("Observe..."));

delay(1000);

for(byte i=0; i<nivel; i++) {

lcd.clear();

lcd.print(F("Memorize:"));

lcd.setCursor(0, 1);

lcd.print(F(">>> "));

lcd.print((char)('A' + seq[i] - 1));

20

lcd.print(F(" <<<"));

delay(800);

lcd.clear();

delay(300);

}

lcd.clear();

lcd.print(F("Sua vez!"));

lcd.setCursor(0, 1);

lcd.print(F("Repita sequenc"));

delay(1500);

pos = 0;

esperando = true;

mostrando = false;

mostrarProg();

}

void mostrarProg() {

lcd.clear();

lcd.print(F("Nivel "));

lcd.print(nivel);

lcd.print(F(" ("));

lcd.print(pos + 1);

lcd.print(F("/"));

lcd.print(nivel);

lcd.print(F(")"));

lcd.setCursor(0, 1);

lcd.print(F("A B C D"));

}

void loopReflexo() {

if (Serial.available() && Serial.read() == '0') {

21

desligar();

return;

}

if (esperando && !fim) {

byte b = 0;

for(byte i=0; i<4; i++) {

if (digitalRead(BTN[i])) {

b = i + 1;

break;

}

}

if (b) {

while(digitalRead(BTN[b-1])) delay(10);

verificarSeq(b);

}

}

}

void verificarSeq(byte b) {

if (b == seq[pos]) {

if (++pos >= nivel) {

ptsTemp += nivel * 10;

lcd.clear();

lcd.print(F("CORRETO! +"));

lcd.print(nivel * 10);

lcd.setCursor(0, 1);

lcd.print(F("Pontos: "));

lcd.print(ptsTemp);

delay(2000);

if (++nivel > 5) finReflexo();

22

else initNivel();

} else mostrarProg();

} else {

lcd.clear();

lcd.print(F("ERROU!"));

lcd.setCursor(0, 1);

lcd.print(F("Fim do jogo"));

delay(2000);

finReflexo(); }}

void finReflexo() {

fim = true;

pontos += ptsTemp;

lcd.clear();

lcd.print(F("Jogo Completo!"));

lcd.setCursor(0, 1);

lcd.print(F("Pontos: "));

lcd.print(ptsTemp);

delay(2000);

pergProx(); }

// ===== TRANSIÇÃO =====

void pergProx() {

lcd.clear();

lcd.print(F("Total: "));

lcd.print(pontos);

lcd.print(F(" pts"));

lcd.setCursor(0, 1);

lcd.print(F("A=Menu C=Final"));

23

while(true) {

if (Serial.available() && Serial.read() == '0') {

desligar();

return;

}

if (lerBtn(0)) { menu(); return; }

if (lerBtn(2)) { telaFinal(); return; }

delay(50);

}

}

// ===== FINAL =====

void telaFinal() {

estado = FINAL;

lcd.clear();

lcd.print(F("PONTUACAO FINAL"));

lcd.setCursor(0, 1);

lcd.print(pontos);

lcd.print(F(" pontos!"));

delay(2500);

lcd.clear();

lcd.print(F("ESCOLHA PREMIO:"));

lcd.setCursor(0, 1);

lcd.print(F("A B C D"));

}

void loopFinal() {

if (Serial.available() && Serial.read() == '0') {

desligar();

return;

}

24

for(byte i=0; i<4; i++) {

if (lerBtn(i)) ativarMotor('A' + i);

}

}

void ativarMotor(char c) {

lcd.clear();

lcd.print(F("OPCAO "));

lcd.print(c);

lcd.setCursor(0, 1);

lcd.print(F("Ativando motor.."));

Serial.write(c);

Serial.flush();

delay(3000);

lcd.clear();

lcd.print(F("Concluido!"));

lcd.setCursor(0, 1);

lcd.print(F("A=Menu"));

while(true) {

if (Serial.available() && Serial.read() == '0') {

desligar();

return;

}

if (lerBtn(0)) {

pontos = 0;

menu();

return;

}

delay(50);

}

25

}

// ===== UTILITÁRIOS =====

bool lerBtn(byte b) {

if (digitalRead(BTN[b])) {

while(digitalRead(BTN[b])) delay(10);

return true;

}

return false;

}

26

Código Arduino Motor

// ARDUINO MOTOR - L293D Control

#define SW 6

// L293D #1 - Motores 1 e 2

#define EN1 2

#define M1A 14

#define M1B 15

#define EN2 5

#define M2A 3

#define M2B 4

// L293D #2 - Motores 3 e 4

#define EN3 10

#define M3A 8

#define M3B 9

#define EN4 13

#define M4A 11

#define M4B 12

const byte EN[] = {EN1, EN2, EN3, EN4};

const byte MA[] = {M1A, M2A, M3A, M4A};

const byte MB[] = {M1B, M2B, M3B, M4B};

byte vel = 255;

bool prev = false;

bool on = false;

void setup() {

Serial.begin(9600);

27

// Config pinos

for(byte i=0; i<4; i++) {

pinMode(EN[i], OUTPUT);

pinMode(MA[i], OUTPUT);

pinMode(MB[i], OUTPUT);

digitalWrite(MA[i], LOW);

digitalWrite(MB[i], LOW);

}

pinMode(SW, INPUT_PULLUP);

delay(100);

// Teste inicial enables

for(byte i=0; i<2; i++) {

analogWrite(EN[i], 255);

delay(50);

analogWrite(EN[i], 0);

}

parar();

Serial.write('0');

Serial.flush();

Serial.println(F("=== PRONTO ==="));

Serial.println(F("Motores 1-2: L293D #1"));

Serial.println(F("Motores 3-4: L293D #2"));

}

void loop() {

// Checa interruptor

bool curr = (digitalRead(SW) == LOW);

if (curr != prev) {

28

on = curr;

Serial.write(on ? '1' : '0');

Serial.flush();

if (!on) parar();

Serial.println(on ? F("ON") : F("OFF"));

prev = curr;

delay(50);

}

// Comandos serial

if (Serial.available()) {

char c = Serial.read();

if (on && c >= 'A' && c <= 'D') {

byte m = c - 'A';

Serial.print(F("Motor "));

Serial.println(m + 1);

ativar(m);

}

}

// Estado periódico

Serial.write(on ? '1' : '0');

delay(200);

}

void ativar(byte m) {

digitalWrite(MA[m], HIGH);

digitalWrite(MB[m], LOW);

analogWrite(EN[m], vel);

29

delay(3000);

analogWrite(EN[m], 0);

digitalWrite(MA[m], LOW);

digitalWrite(MB[m], LOW);

}

void parar() {

for(byte i=0; i<4; i++) {

analogWrite(EN[i], 0);

digitalWrite(MA[i], LOW);

digitalWrite(MB[i], LOW);

}

}

30

### 2.5 Manual de Operação Básico

Para Ligar o Sistema:

Conectar fonte à tomada

Acionar interruptor

Aguardar mensagem "SISTEMA LIGADO!"

Sistema entra no Menu Principal automaticamente

Para Jogar Quiz:

No menu, pressionar botão A

Ler pergunta no LCD (mostrada em 2 partes)

Pressionar A para Verdadeiro ou B para Falso

Pressionar C para próxima pergunta

Ao final de 10 perguntas, escolher entre Menu ou Final

Para Jogar Memória:

No menu, pressionar botão B

Observar sequência mostrada

Repetir sequência pressionando botões

Avançar pelos níveis até errar ou completar 5 níveis

Ao final, escolher entre Menu ou Final

Para Receber Prêmio:

Na tela final, verificar pontuação

Pressionar botão do prêmio desejado (A, B, C ou D)

Aguardar 3 segundos (motor acionando)

Retirar brinde da bandeja inferior

Pressionar A para voltar ao menu ou desligar

Para Desligar:

Desligar interruptor

Display apaga

Sistema desliga


31

### 2.6 CRONOGRAMA MACRO


32

### 2.7 CRONOGRAMA MACRO

33

### 3 REFERÊNCIAS

ARDUINO. Arduino Uno Rev3. Arduino Official Documentation, 2024.

Disponível em: https://www.arduino.cc/en/Main/ArduinoBoardUno.

ARDUINO. LiquidCrystal Library Reference. Arduino Official

Documentation, 2024. Disponível em:

https://www.arduino.cc/en/Reference/LiquidCrystal

ATMEL. ATmega328P Datasheet. Atmel Corporation, 2015. Disponível em:

http://www.atmel.com.

BANZI, Massimo; SHILOH, Michael. Primeiros passos com o Arduino. 2.

ed. São Paulo: Novatec, 2015.

INSTRUCTABLES. Otto DIY - Build You Own Robot in Two Hours.

Disponível em: https://www.instructables.com/Otto-Build-You-Own-Robot-in-

Two-Hours/. (https://www.instructables.com/Otto-Build-You-Own-Robot-in-Two-Hours/)

MARGOLIS, Michael. Arduino cookbook. 3. ed. Sebastopol: O'Reilly

Media, 2020.

MCROBERTS, Michael. Arduino básico. São Paulo: Novatec, 2011.

MONK, Simon. Programação com Arduino: começando com sketches.

2. ed. Porto Alegre: Bookman, 2017.

TEXAS INSTRUMENTS. L293D Quadruple Half-H Driver Datasheet.

Texas Instruments, 2016. Disponível em: http://www.ti.com.

Material didático do Curso Superior de Tecnologia em Manufatura

Avançada. FATEC São José dos Campos, 2023-2024.

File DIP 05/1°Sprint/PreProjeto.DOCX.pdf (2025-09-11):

CURSO SUPERIOR DE TECNOLOGIA EM MANUFATURA AVANÇADA

PRÉ-PROJETO DE DESENVOLVIMENTO INTEGRADO DE PRODUTO: MÁQUINA INTERATIVA GRAB & CATCH

JOÃO PEDRO DA SILVA ROSA
JOÃO VITOR MORAIS SOUZA
GABRIEL ALVES

São José dos Campos
2024

1.INTRODUÇÃO

O presente pré-projeto tem como objetivo desenvolver uma máquina interativa de brindes para ser utilizada em eventos e apresentações institucionais. Diferente de uma máquina de vendas convencional, esta solução busca engajar os visitantes por meio de jogos, quizzes e desafios interativos, recompensando-os com brindes institucionais da FATEC.

O projeto envolve aspectos técnicos de sistemas embarcados, interfaces de usuário via tela touch, sensores e atuadores para liberação dos brindes, além de elementos de design atrativo inspirado em máquinas de vendas caseiras.

## 1.1.Justificativa

O desenvolvimento desta máquina interativa atende a uma demanda crescente por soluções inovadoras de marketing educacional e tecnológico.

- Relevância para a instituição: a máquina reforça a
imagem da FATEC como referência em inovação e tecnologia, promovendo a instituição em feiras, eventos e visitas escolares.
- Impacto no público: proporciona uma experiência divertida e memorável, associando a marca da instituição a momentos positivos.
- Contribuição acadêmica: o projeto possibilita aplicação prática de conceitos de manufatura avançada, automação, eletrônica e design, servindo como experiência integradora para os alunos.

2

## 1.2.Objetivos geral e específicos

### Objetivo Geral

Desenvolver uma máquina interativa com sistemas embarcados para

proporcionar experiências lúdicas em eventos, promovendo a marca

FATEC por meio de brindes gratuitos.

### Objetivos Específicos

- Pesquisar referências de máquinas de vendas interativas e design atrativo para adaptação ao projeto.
- Desenvolver a interface de interação em tela touch, incluindo quizzes e mini-jogos.
- Implementar sensores e motores responsáveis pela liberação dos brindes.
- Projetar a estrutura física da máquina com foco em baixo custo e facilidade de manutenção.
- Realizar testes de fluxo de usuários, limitando tempo de interação e garantindo reabastecimento rápido.

### 1.3. Proposta de design e funcionalidade da solução

A máquina terá design semelhante a uma máquina de vendas caseira, porém adaptada para interação gratuita.

3

Componentes principais:

Materiais | Quantidade | Tamanho | Preço Unitário | Preço Total
Arduino UNO | 1 | 68,6mm x 53,4mm | R$ 49,90 | R$ 49,90
Motor de passo NEMA 17 | 2 42mm x 42mm x | 34mm | R$ 64,90 | R$ 129,80
Driver A4988 | 2 | 15,3mm x 20,3mm | R$ 16,90 | R$ 33,80
Servo Motor SG90 | 2 | 23X 12.1X 21.4mm | R$ 12,50 | R$ 25,00
Display LCD 16X2 | 1 | 64,5mm x 16mm | R$ 37,90 | R$ 37,90
Sensor IR | 2 | 32mm x 14mm | R$ 6,90 | R$ 13,08
Teclado matricial 4X4 | 1 77mm x 70mm x | 0,8mm | R$ 6,50 | R$ 6,50
Estrutura (MDF/Acrílico) | 1 | — | — | —
Toral Estimado | R$ 296,70

Coqui inicial da máquina interativa:

4


Imagens de referências tiradas da internet:


Funcionalidades:


- Jogos rápidos (quiz institucional, mini games de tempo, desafios relâmpago).

5

- Sistema de recompensa imediata com brindes como figurinhas, chaveiros e lembretes de eventos.
- Mensagens interativas ao final da interação (ex.: frases motivacionais ou links para cursos da instituição).
- Controle de tempo por usuário (30s a 1 min) para evitar filas longas.

### 1.4. Cronograma

O cronograma macro que foi feito para a primeira sprint.


### 1.5. Resultados esperados

Espera-se que o projeto resulte em uma máquina interativa funcional, capaz de:

- Atrair visitantes em eventos por meio da gamificação.
- Promover a FATEC de forma criativa, tecnológica e inovadora.

6

- Distribuir brindes de maneira rápida, prática e divertida.
- Servir como modelo para futuras aplicações de interação homem-máquina no contexto educacional.

REFERÊNCIAS

- https://www.youtube.com/watch?v=F640XI3sGWM
- https://www.youtube.com/watch?v=BHQBsswUeT0
- https://blog.eletrogate.com/maquina-de-vendas-automatica-com-rfid-e-nodemcu/
- https://www.youtube.com/watch?v=EYs-DGWmH5A

Imagem 1: Referência da internet

7


Imagem 2: Referência da internet

Imagem 2: Referência da internet

8

Imagem 4: Referência da internet

9

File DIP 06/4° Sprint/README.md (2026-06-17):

# Cronograma Micro - Entrega 4
 
| 📅 Data | 📝 Tarefa | 🔍 Detalhamento | 👤 Responsável |
|---|---|---|---|
| 09/05/2026 | Início da montagem dos eletrônicos | Separação e organização dos componentes eletrônicos para montagem | Equipe |
| 10/05/2026 | Montagem dos eletrônicos — fase 1 | Instalação dos componentes principais e primeiras conexões | Equipe |
| 12/05/2026 | Montagem dos eletrônicos — fase 2 | Finalização das conexões e verificação do cabeamento | Equipe |
| 09/05/2026 | Início da integração do sistema mecânico | Revisão das peças estruturais e início da fixação na estrutura | João Pedro |
| 12/05/2026 | Integração mecânica — continuação | Ajuste de encaixes e verificação de alinhamento estrutural | João Pedro |
| 15/05/2026 | Conclusão do sistema mecânico na estrutura | Conferência final da integridade mecânica e fixações | João Pedro |
| 10/05/2026 | Início dos testes de validação | Definição dos critérios de validação e primeiros testes funcionais | Equipe |
| 13/05/2026 | Testes de validação — fase intermediária | Testes combinando sistemas eletrônico e mecânico integrados | Equipe |
| 16/05/2026 | Conclusão dos testes de validação | Registro de resultados e identificação de pontos de ajuste | Equipe |
| 16/05/2026 | Início dos ajustes técnicos | Correção de falhas identificadas nos testes de validação | Equipe |
| 17/05/2026 | Ajustes técnicos — continuação | Refinamento de parâmetros e reteste dos pontos críticos | Equipe |
| 18/05/2026 | Conclusão dos ajustes técnicos | Validação final após ajustes e aprovação para entrega | Equipe |
| 09/06/2026 | Início da documentação e da apresentação | Estruturação dos tópicos e definição do roteiro de apresentação | Equipe |
| 10/06/2026 | Redação da documentação final | Escrita e formatação do relatório e slides | Equipe |
| 11/06/2026 | Revisão e entrega | Revisão geral, correções finais e submissão da Entrega 4 | Equipe |

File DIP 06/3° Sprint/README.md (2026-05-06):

# Cronograma Micro — Entrega 3

| 📅 Data | 📋 Tarefa | 🔍 Detalhamento | 👤 Responsável |
|---|---|---|---|
| 13/04/2026 | Início da montagem da estrutura da máquina | Levantamento dos materiais e início da montagem física dos componentes principais | Equipe |
| 17/04/2026 | Montagem parcial e verificação estrutural | Continuação da montagem e conferência do alinhamento e fixação das peças | Equipe |
| 22/04/2026 | Início da programação dos jogos | Estruturação do código base e definição da lógica dos jogos para a máquina | João Pedro |
| 22/04/2026 | Visualização e testes de programação | Execução dos testes iniciais do código e validação visual do funcionamento dos jogos | João Pedro |
| 25/04/2026 | Ajustes no código e correção de bugs | Correção de erros identificados nos testes e melhoria de performance | João Pedro |
| 28/04/2026 | Testes integrados (software + hardware) | Testes combinando a programação com a estrutura física montada | Equipe |
| 01/05/2026 | Validação final da integração | Conferência completa do funcionamento da máquina com os jogos instalados | Equipe |
| 04/05/2026 | Conclusão da montagem e programação | Finalização dos ajustes físicos e salvamento das versões finais do código | Equipe |
| 25/04/2026 | Início da finalização do projeto executivo | Revisão das medições, integração dos subsistemas e consolidação dos arquivos técnicos | João Pedro |
| 25/04/2026 | Consolidação dos documentos técnicos | Conferência e unificação dos desenhos, diagramas e demais arquivos do projeto executivo | João Pedro |
| 05/05/2026 | Início da documentação e da apresentação | Estruturação dos tópicos e definição do roteiro da apresentação | Equipe |
| 05/05/2026 | Redação da documentação final | Escrita e formatação do relatório e dos slides | Equipe |
| 06/05/2026 | Revisão geral da documentação | Correções finais, preparação dos anexos e ensaio da apresentação | Equipe |
| 06/05/2026 | Apresentação e entrega | Ensaio final e submissão da Entrega 3 | Equipe |

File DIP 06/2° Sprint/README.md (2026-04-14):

## Cronograma Micro - Entrega 2

| 📅 **Data** | 📝 **Tarefa** | 🔍 **Detalhamento** | 👤 **Responsável** |
| --- | --- | --- | --- |
| **15/03/2026** | Início da pesquisa sobre a parte mecânica da mola | Levantamento de referências e materiais sobre o mecanismo de mola | João Vitor & Gabriel |
| **17/03/2026** | Análise dos parâmetros mecânicos | Estudo de rigidez, compressão e dimensionamento da mola | João Vitor & Gabriel |
| **19/03/2026** | Consolidação da pesquisa mecânica | Organização dos dados e conclusões sobre a parte mecânica | João Vitor & Gabriel |
| **20/03/2026** | Entrega da pesquisa mecânica | Revisão final e registro dos resultados obtidos | João Vitor & Gabriel |
| **16/03/2026** | Início da pesquisa sobre programação do LCD TFT | Levantamento de bibliotecas e documentação do display LCD TFT | João Pedro |
| **18/03/2026** | Estudo da comunicação com o LCD TFT | Análise do protocolo de comunicação e testes iniciais de código | João Pedro |
| **19/03/2026** | Implementação de testes básicos no LCD TFT | Primeiros testes de exibição e validação do funcionamento | João Pedro |
| **20/03/2026** | Consolidação da pesquisa do LCD TFT | Documentação dos resultados e definição da abordagem de programação | João Pedro |
| **18/03/2026** | Início do desenvolvimento do Desenho Técnico Atualizado | Revisão do desenho anterior e definição das atualizações necessárias | João Vitor |
| **23/03/2026** | Desenvolvimento das vistas e cortes | Elaboração das vistas técnicas, cortes e detalhamentos do projeto | João Vitor |
| **30/03/2026** | Revisão e ajustes do desenho técnico | Correções de cotas, tolerâncias e normas técnicas | João Vitor |
| **05/04/2026** | Finalização do desenho técnico | Revisão final e exportação do arquivo técnico atualizado | João Vitor |
| **08/04/2026** | Entrega do Desenho Técnico Atualizado | Validação e submissão do desenho técnico final | João Vitor |
| **26/03/2026** | Elaboração da Minuta do Projeto Finalizado | Estruturação e redação da minuta com os dados consolidados do projeto | João Pedro |
| **26/03/2026** | Revisão e entrega da Minuta | Revisão final e submissão da minuta do projeto | João Pedro |
| **09/04/2026** | Início da Documentação e Apresentação | Estruturação dos tópicos e definição do roteiro da apresentação | Equipe |
| **09/04/2026** | Montagem dos slides e relatório final | Elaboração dos slides e redação do relatório final da entrega | Equipe |
| **09/04/2026** | Revisão geral e entrega | Revisão final da documentação e submissão da Entrega 2 | Equipe |

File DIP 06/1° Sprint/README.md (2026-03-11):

# 🔬 Cronograma Micro — Entrega 1

| 📅 **Data** | 📝 **Tarefa** | 🔍 **Detalhamento** | 👤 **Responsável** |
|---|---|---|---|
| **25/02/2026** | Formalização das Equipes | Definição oficial dos membros, papéis e responsabilidades de cada colaborador no projeto | João Pedro |
| **28/02/2026** | Início da pesquisa de materiais | Levantamento inicial de fornecedores e especificações técnicas dos materiais necessários | João Vitor & Gabriel |
| **03/03/2026** | Consolidação da pesquisa de materiais | Comparativo de preços, seleção de fornecedores e registro das especificações finais | João Vitor & Gabriel |
| **28/02/2026** | Início da pesquisa sobre LCD TFT | Estudo de modelos compatíveis e protocolos de comunicação com microcontroladores | João Pedro & Gabriel |
| **04/03/2026** | Conclusão da pesquisa sobre LCD TFT | Definição do modelo escolhido e documentação das especificações de integração | João Pedro & Gabriel |
| **28/02/2026** | Início da pesquisa sobre Microcontroladores | Comparativo entre opções disponíveis: GPIOs, memória e compatibilidade com o projeto | João Pedro & Gabriel |
| **03/03/2026** | Conclusão da pesquisa sobre Microcontroladores | Seleção do microcontrolador e registro das justificativas técnicas da escolha | João Pedro & Gabriel |
| **03/03/2026** | Início da pesquisa de iluminação | Estudo de tipos de LEDs, controladores e esquemas de acionamento para a máquina | Gabriel |
| **07/03/2026** | Testes de integração de iluminação | Montagem de protótipo simples e validação do esquema de acionamento escolhido | Gabriel |
| **11/03/2026** | Conclusão da pesquisa de iluminação | Documentação final com circuito definido e componentes selecionados | Gabriel |
| **08/03/2026** | Início da consolidação do Pré-Projeto | Reunião de alinhamento e integração de todas as pesquisas realizadas pela equipe | João Vitor |
| **10/03/2026** | Pré-Projeto Finalizado | Documento técnico completo com decisões de design, componentes e arquitetura do sistema | João Vitor |
| **12/03/2026** | Elaboração da documentação e apresentação | Estruturação dos tópicos, redação do relatório e montagem dos slides finais | Equipe |
| **12/03/2026** | Revisão e entrega | Revisão geral, ensaio da apresentação e submissão da Entrega 1 | Equipe |

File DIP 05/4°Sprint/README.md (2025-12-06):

## Cronograma Micro - Entrega 4

| 📅 **Data** | 📝 **Tarefa** | 🔍 **Detalhamento** | 👤 **Responsável** | ⏳ **Início** | ⏳ **Fim**  |
| --- | --- | --- | --- | --- | --- |
| **24/11/2025** | Finalização da Caixa | Ajustes finais na caixa e conferência dos componentes | João Vítor | 24/11/2025 | 25/11/2025 |
| **16/11/2025** | Correção do Projeto Executivo  | Revisão e ajustes no projeto executivo, correções de medições | João Pedro | 16/11/2025 | 16/11/2025 |
| **20/11/2025** | Finalização da Máquina | Finalização da montagem da máquina e testes gerais | Equipe | 20/11/2025 | 27/11/2025 |
| **20/11/2025** | Finalização do Relatório Final | Revisão e conclusão do relatório final para entrega | João Vítor | 20/11/2025 | 27/11/2025 |
| **26/11/2025** | Documentação e Apresentação | Elaboração do conteúdo da documentação e montagem da apresentação | Equipe | 26/11/2025 | 27/11/2025 |

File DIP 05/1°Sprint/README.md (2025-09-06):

## Cronograma Micro - Entrega 1 

| 📅 Data | ✅ Tarefa | 📝 Detalhamento | 👤 Responsável |  
|---|---|---|-----|
| **18/08 (Seg)** | Formalização das equipes| Reunião inicial para definir membros | Equipe |
| | Pesquisa de mercado  | Definição do escopo e levantamento inicial | João Vitor & Gabriel |
| | Levantamento inicial de materiais | Listar insumos e componentes para estimativa de custos | João Pedro |
| | Continuação da pesquisa | Pesquisa de dados secundários e fontes relevantes | João Vitor & Gabriel |
| **21/08 (Qui)** | Início do Pré-Projeto | Estruturação inicial do pré-projeto (esboço, objetivos) | João Vitor  |
| **22/08 (Sex)** | Pesquisa de mercado | Análise detalhada da concorrência, público-alvo e diferenciais | João Vitor & Gabriel |
| **25/08 (Seg)** | Organização da pesquisa | Estruturação e síntese dos dados coletados | João Vitor & Gabriel |
| | Pesquisa de preços | Contato e cotação com fornecedores | João Pedro  |
| **28/08 (Qui)** | Início do croqui inicial  | Esboço manual ou digital das primeiras ideias | Equipe |
| | Consolidação da equipe | Documentação da formalização da equipe | Equipe |
| **29/08 (Sex)** | Desenvolvimento do croqui | Refinamento do croqui e discussão para melhorias | Equipe |
| **30/08 (Sáb)** | Finalização da pesquisa de mercado  | Relatório visual e texto resumo | João Vitor & Gabriel |
| **31/08 (Dom)** | Escolha do croqui final | Decisão sobre a melhor versão para seguir | Equipe |
| **01/09 (Seg)** | Apresentação do croqui final | Digitalização e organização do arquivo | Equipe |
| | Início da apresentação | Definir tópicos, estrutura | Equipe |
| **02/09 (Ter)** | Finalização da estimativa de preços | Criação de planilha detalhada com preços e fornecedores  | João Pedro |
| **03/09 (Qua)** | Desenvolvimento do Pré-Projeto | Redação completa, revisão e ajustes finais | João Vitor |
| **05/09 (Sex)** | Criação dos slides | Montagem do conteúdo e diagramação inicial dos slides | Equipe |
| **06/09 (Sáb)** | Design da apresentação | Inserção de imagens, gráficos e organização visual | Equipe |
| **07/09 (Dom)** | Revisão final do Pré-Projeto | Última revisão antes da entrega | João Vitor |
| **08/09 (Seg)** | Revisão final da apresentação | Checagem de conteúdo, revisão textual e visual | Equipe |
| **09/09 (Ter)** | Ensaio da apresentação | Treino coletivo e divisão de falas | Equipe |
| **10/09 (Qua)** | Entrega final | Submissão do pré-projeto, documentação e apresentação | Equipe |

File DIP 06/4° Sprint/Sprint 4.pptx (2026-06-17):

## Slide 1

Grab&Catch

4 Sprint

Professor:

DAWILMAR

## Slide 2

nOSSA EQUIPE


joão Vitor

MECÂNICA/ELETRÔNICA

João pEDRO

PROGRAMAÇÃO/ELETRÔNICA

GABRIEL Alves

MECÂNICA/ELETRÔNICA

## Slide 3

Sumário

01

02

03

04

05

Sobre Nosso Projeto

Atividades Realizadas

Setor Programação

Teste de Integração Eletromecânica

Estrutura do Protótipo

06

07

08

Cronograma

09

Conclusão

Regras do Projeto

Objetivos da Sprint 3

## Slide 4


01

sOBRE NOSSO PROJETO

A Grab & Catch é uma máquina interativa que distribui brindes para quem interage com seus jogos. Neste semestre, o projeto visa transformar a prova de conceito apresentada na Feira de Soluções em um protótipo com melhorias na estrutura, eletrônica e programação.

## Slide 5

02

Atividades Realizadas

Finalização da integração dos componentes da parte mecânica

Desenvolvimento da Regra do nosso Projeto

Realização dos testes do produto nas molas

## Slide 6

Trabalhos realizados
- setor programação


03


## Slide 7

Teste de Integração Eletromecânica


04


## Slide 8

05

Estrutura do Protótipo


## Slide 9

06

Regras do projeto

Respeitar as vezes dos outros jogadores

Cada participante terá duas tentativas

Seguir as orientações dos responsaveis

Não pode pedir ajuda, trapacear e cada jogo é singular

Os competidores tem o direito a apenas um brinde

Caso seja pego quebrando as regras será desqualificado

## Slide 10

Objetivos da Sprint 4

A 4ª sprint foi marcada pela finalização da integração dos componentes da parte mecânica e pelo desenvolvimento da regra do nosso projeto. Além disso, a etapa englobou a realização dos testes do produto nas molas, garantindo o avanço das validações práticas do protótipo.

07

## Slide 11

cronograma

08

2

4

Teste de Validação

16/05/2026

Finalização do Relatorio Final

09/06/2026

Montagem dos eletrônicos
+sistema mecânico na estrutura

15/05/2026

1

Ajustes Tecnicos

18/05/2026

3

5

Apresentação

11/06/2026

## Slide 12


conclusão


Nosso GitHub (https://github.com/JaoRosa12/Grab-Catch-Maquina-Interativa?tab=readme-ov-file)

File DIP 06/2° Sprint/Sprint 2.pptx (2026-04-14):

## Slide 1

Grab&Catch

2 Sprint

Professor:

DAWILMAR

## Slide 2

nOSSA EQUIPE


joão Vitor

MECÂNICA/ELETRÔNICA

João pEDRO

PROGRAMAÇÃO/ELETRÔNICA

GABRIEL Alves

MECÂNICA/ELETRÔNICA

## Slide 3

Sumário

01

02

Melhorias

03

04

05

Sobre Nosso Projeto

Desenho Estrutural

Conjunto mecânico

Acoplamento da mola

06

07

08

Objetivos

09

Cronograma

10

conclusão

Setor Programação

Novos Jogos

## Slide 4


01

sOBRE NOSSO PROJETO

A Grab & Catch é uma máquina interativa que distribui brindes para quem interage com seus jogos. Neste semestre, o projeto visa transformar a prova de conceito apresentada na Feira de Soluções em um protótipo com melhorias na estrutura, eletrônica e programação.

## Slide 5

02

MELHORIAS

Substituição do display LCD por tela TFT Touch colorida

Desenvolvimento de novos jogos interativos (Jogo da Velha, Pong)

Aprimoramento do sistema mecânico de mola e redesign da estrutura física

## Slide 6

Desenho Estrutural (CAD)

03


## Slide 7

Conjunto mecânico

04


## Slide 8

Acoplamento da mola


05

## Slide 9

Trabalhos realizados
- setor programação


06

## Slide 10

Trabalhos realizados
- setor programação


06

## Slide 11


Trabalhos realizados
- setor programação

06

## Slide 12

novos jogos

07

JOGO DA VELHA


PONG


JOGO DA MEMORIA


QUIZ


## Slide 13

Objetivos da Sprint 2

Nesta sprint, o foco foi no avanço no desenvolvimento da programação do LCD TFT e no conjunto mecânico em que a mola agiria, sendo feitos testes físicos em ambos para determinar funcionabilidade. Nestes testes foram alinhados alguns parâmetros para o desenvolvimento da estrutura do produto, que comportará estes componentes.

08

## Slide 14

09

cronograma

2

4

Pesquisa sobre a progrmação do LCD TFT

16/03/2026

Minuta do Projeto

26/03/2026

Pesquisa sobre a parte mecanica da mola

15/03/2026

1

Desenvolvimento do Desenho Tecnico

18/03/2026

3

5

Apresentação

09/04/2026

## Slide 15


conclusão


Nosso GitHub (https://github.com/JaoRosa12/Grab-Catch-Maquina-Interativa?tab=readme-ov-file)

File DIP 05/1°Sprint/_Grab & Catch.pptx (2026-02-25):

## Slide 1

Grab & Catch

Integrantes: João Pedro da Silva Rosa
João Vitor Morais Souza
Gabriel Alves

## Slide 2

Índice


01

Introdução

05

Estimativa de Custos

02

Objetivo

Cronograma

06

03

07

04

Croqui

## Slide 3

Com o avanço da tecnologia, a automação tem se tornado cada vez mais presente no nosso dia a dia. Pensando nisso, este projeto tem como proposta desenvolver uma máquina interativa, com baixo custo de produção, que seja prática e interativa para o usuário, além de promover a instituição FATEC.
A ideia é criar uma solução simples, funcional e acessível para ambientes como escolas, empresas ou eventos.

Introdução

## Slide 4


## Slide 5


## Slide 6

Objetivo

O principal objetivo do projeto é criar uma máquina automatizada que funcione de forma interativa, por exemplo, o usuário responde algumas perguntas e, se acertar tudo, pode escolher um produto. Além disso, o sistema será planejado para facilitar a reposição dos itens e garantir a segurança e manutenção do equipamento.

O projeto será feito por etapas, com testes em cada módulo antes da montagem final, sempre com apoio dos orientadores e seguindo um cronograma de desenvolvimento.

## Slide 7


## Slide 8


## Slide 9


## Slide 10


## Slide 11

Esse projeto busca mostrar como é possível unir tecnologia e criatividade para resolver problemas do dia a dia de forma simples e barata. A máquina automatizada tem potencial para ser usada em vários lugares. Além disso, o desenvolvimento do projeto ajuda a aplicar na prática os conhecimentos vistos ao longo do curso.

Conclusão

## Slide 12

PESQUISA DE SITES ESCOLARES

  - https://www.youtube.com/watch?v=F640XI3sGWM
  - https://www.youtube.com/watch?v=BHQBsswUeT0
  - https://blog.eletrogate.com/maquina-de-vendas-automatica-com-rfid-e-nodemcu/
  - https://www.youtube.com/watch?v=EYs-DGWmH5A

Pesquisas


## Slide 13

GitHub


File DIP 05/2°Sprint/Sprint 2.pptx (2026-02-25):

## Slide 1

Grab & Catch

MAQUINA INTERATIVA

GABRIEL ALVES.
JOÃO PEDRO.
JOÃO VITOR.

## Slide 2


Sumário

Mapa Mental;
Esquema de Montagem;
Simulação;
Programação;
Lista de Matérias;
Croqui (Sprint 1);
Desenho Técnico (Catia);
Cronograma;
Conclusão.

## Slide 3


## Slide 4

Esquema de Montagem


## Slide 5

Simulação


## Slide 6

Programação Motor


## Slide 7

Programação Interface


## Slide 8

Programação Interface


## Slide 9

Programação Interface


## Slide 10

Lista de Matériais


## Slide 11


Croqui (Sprint 1)

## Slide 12

Desenho Técnico (Catia)


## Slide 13

Cronograma


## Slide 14

Conclusão

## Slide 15


GitHub

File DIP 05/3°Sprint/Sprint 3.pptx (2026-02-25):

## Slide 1


Manufatura Avançada

Grab & Catch

Aluno: João Pedro da Silva Rosa
João Vitor Morais Souza
Gabriel Alves
Professora: Danielle

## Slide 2

Cronograma

Índice

03

Moteres

Teste dos Motores

LCD 16X2

07

Teste das Molas

Regras

11

04

08

12

Conclusão

05

09

Fluxograma

Estimativa de Materiais

06

Teste do LCD

10

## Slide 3

Motores


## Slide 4


Teste dos

Motores


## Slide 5

LCD 16X2


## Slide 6


Teste do

LCD 16X2


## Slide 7

Teste da Mola


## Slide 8

Regras

Cada game tem 10 fasase que vale 10 pontos (1 ponto cada),
Para ganhar o Premio mais simples é necessário ganhar 6 pontos no mínimo, e para o Premio Plus é 8 pontos no minimo
Não pode pedir ajuda, trapacear e cada jogo é singular
Caso seja pego quebrando as regras será desqualificado
Cada jogador terá limite de 3 minutos para os jogos
Cada um tem direito a um brinde

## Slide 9

Fluxograma

Principal


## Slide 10

Fluxograma

Principal


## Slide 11

Fluxograma

Principal

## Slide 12

Estimativa de Materiais


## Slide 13

Cronograma


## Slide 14


Conclusão

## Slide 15

QR Code - GitHub


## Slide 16

Muito Obrigado!

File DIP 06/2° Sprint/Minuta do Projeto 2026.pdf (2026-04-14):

## CURSO SUPERIOR DE TECNOLOGIA EM

## MANUFATURA AVANÇADA

## MINUTA DE PROJETO DE DESENVOLVIMENTO INTEGRADO DE PRODUTO V – MAQUINA INTERATIVA

João Pedro da Silva Rosa

João Vitor Moraes de Sousa

Gabriel Alves da Silva

ESCOPO DO PROJETO

O projeto consiste na continuação do desenvolvimento da Máquina Interativa Grab & Catch. A primeira versão foi apresentada na Feira de Soluções como prova de conceito, porém apresentou limitações estruturais e mecânicas. Nesta nova etapa, serão aplicadas melhorias no design, na estrutura e no sistema de funcionamento da máquina, tornando o protótipo mais robusto, funcional e adequado para uso em eventos institucionais.

O projeto será subdividido em 3 partes principais de desenvolvimento, sendo:

Eletrônica;

Programação;

Estrutural.

As principais melhorias previstas em relação ao protótipo anterior incluem:

Desenvolvimento de novos jogos;

Melhoria do sistema mecânico de mola para liberação dos brindes;

Reorganização e otimização do sistema eletrônico baseado em Arduino;

Substituição do display LCD por tela TFT Touch colorida.


Fonte: Autor próprio

O objetivo do sistema é oferecer uma interface de interação com o usuário por meio de tela TFT Touch, na qual o usuário participa de jogos rápidos. Ao atingir a pontuação necessária, o sistema aciona os motores DC responsáveis pela liberação do brinde escolhido.

Abaixo, a estrutura desenvolvida no CATIA no semestre passado:


Fonte: Autor próprio.

Estrutura apresentada na Feira de Soluções no semestre passado:


Fonte: Autor próprio.

CRONOGRAMA MACRO


Fonte: Autor próprio.

ESCOPO DO PRODUTO

O produto final consiste em uma versão aprimorada da Máquina Interativa Grab & Catch, mantendo o conceito original de engajamento do público por meio de jogos com recompensa em brindes. As melhorias aplicadas nesta etapa buscam corrigir os problemas identificados no prova de conceito, tornando a solução mais confiável e adequada para utilização em eventos institucionais da FATEC.

Espera-se que o produto final seja capaz de:

Atrair visitantes em eventos por meio de novos jogos interativos;

Oferecer uma interface mais intuitiva e atrativa com tela TFT Touch

colorida;

Apresentar estrutura física resistente e de fácil manutenção.


Fonte: Autor próprio.

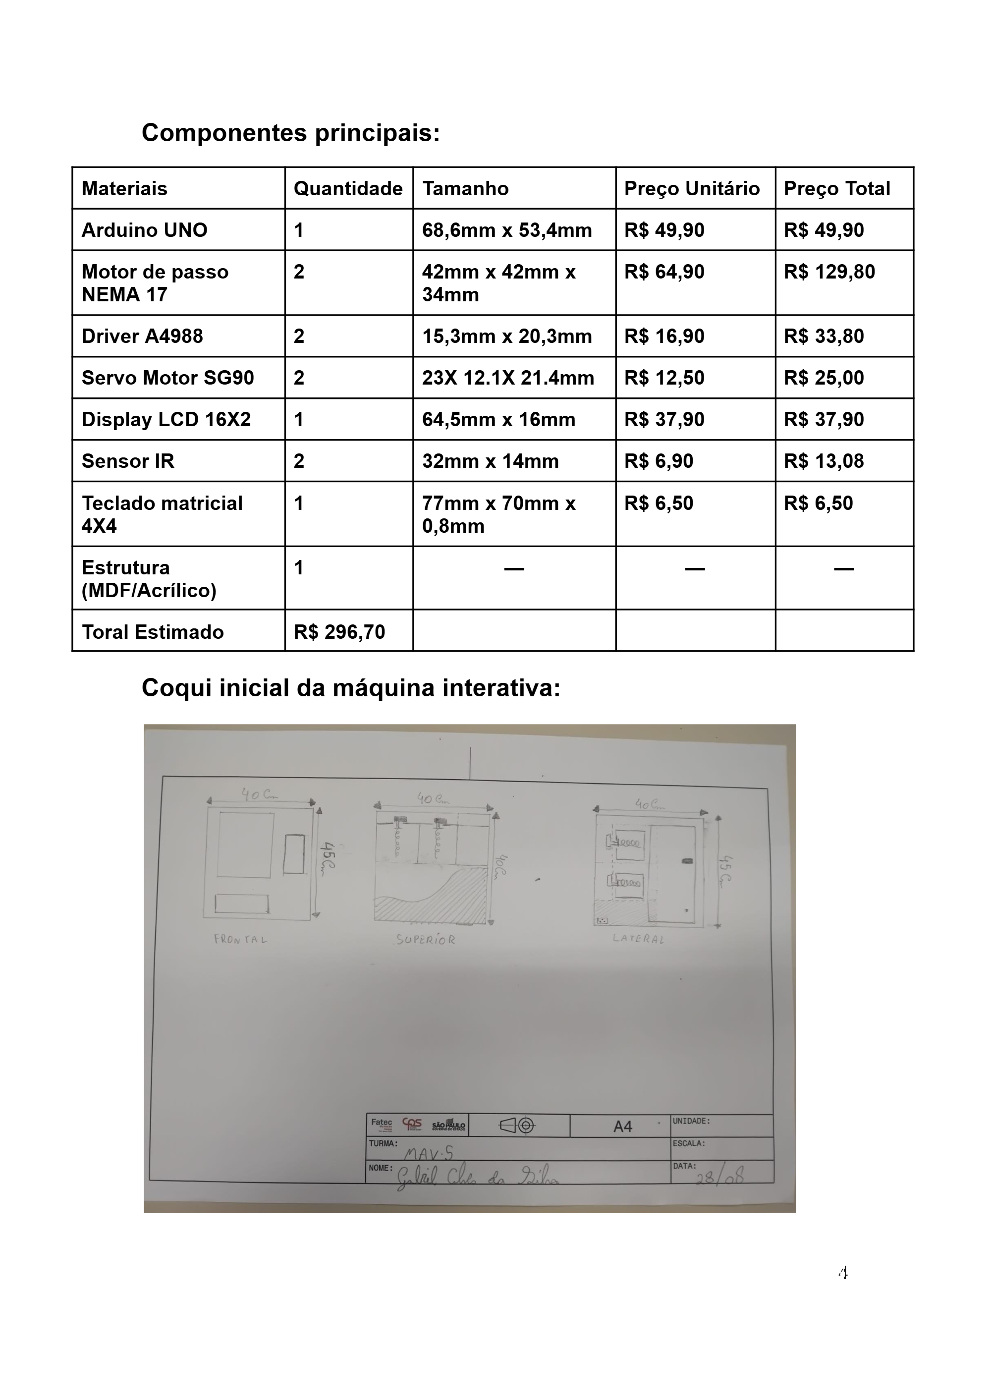
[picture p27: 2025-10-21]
DIP 05/1°Sprint/download.png

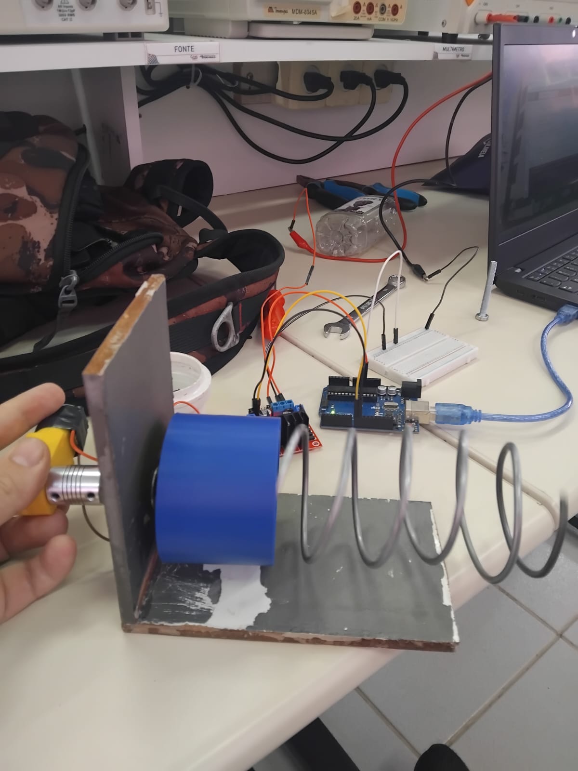
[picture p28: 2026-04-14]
DIP 06/2° Sprint/mola e acoplamento.jpeg

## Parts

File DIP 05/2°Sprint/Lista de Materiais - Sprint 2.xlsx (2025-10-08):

Estimativa de Materiais - Maquinas Interativa
Materiais | Quantidade Necessária | Tamanho | Preço Unitário | Preço Total | Link
Arduino Uno | 1 | 68,6 mm × 53,4 mm | R$49.90 | R$49.90 | Arduino UNO (https://www.eletrogate.com/uno-r3-cabo-usb-para-arduino)
Motor DC | 4 | 70 mm × 22 mm × 18 mm | R$7.90 | R$31.60 | Motor DC
Driver A4988 | 2 | 15,3 mm × 20,3 mm | R$16.90 | R$33.80 | Driver Motor de Passo A4988 com Dissipador de Calorr (https://www.eletrogate.com/driver-motor-de-passo-a4988-c-dissipador-de-calor)
Servomotor SG90 | 2 | 23x12.1x21.4mm | R$12.50 | R$25.00 | Servomotor (https://www.robocore.net/servo-motor/micro-servo-9g-sg90-towerpro)
Tela Display TFT 2.4 | 1 | 71,5mm x 52mm. | R$59.90 | R$59.90 | Tela Display TFT
Sensor IR | 2 | 32mm x 14mm | R$6.90 | R$13.80 | Sensor IR (https://www.eletrogate.com/sensor-de-obstaculo-reflexivo-infravermelho)
Teclado matricial 4x4 | 1 | 77 mm × 70 mm × 0,8 mm | R$6.50 | R$6.50 | Teclado Matricial (https://www.robocore.net/botao-chave/teclado-matricial-de-membrana-16-teclas)
Arduino Mega | 1 | 53.36 × 101,86mm | R$189.90 | R$189.90 | Arduino Mega
Ponte H L298N | 2 | 43x43x27mm | R$18.90 | R$37.80 | https://www.eletrogate.com/ponte-h-dupla-l298n
Estrutura (MDF/Acrílico) | 1 | - | - | - | -
Total Estimado | R$448.20

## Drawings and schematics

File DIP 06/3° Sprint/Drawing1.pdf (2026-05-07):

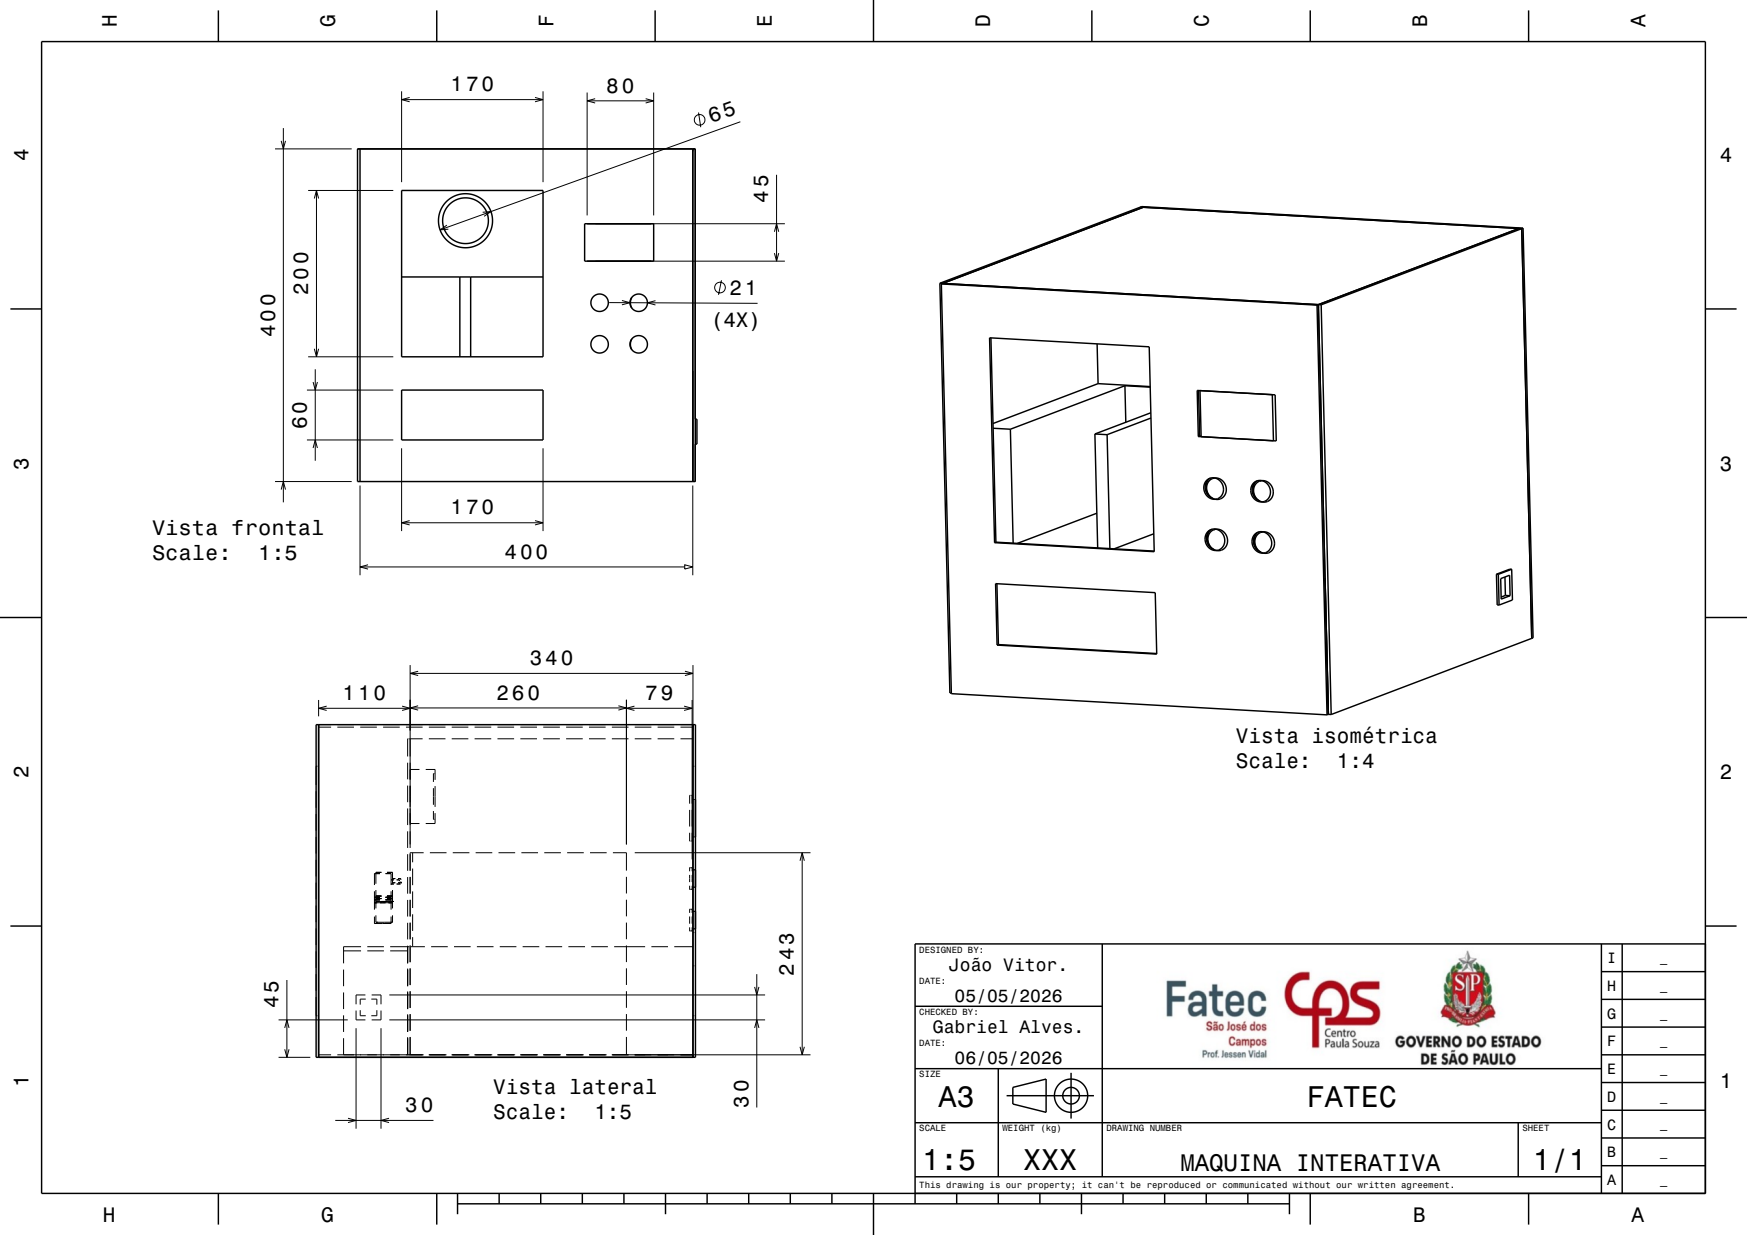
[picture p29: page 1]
CHECKED BY: Gabriel Alves.; Vista isométrica Scale: 1:4; Vista frontal Scale: 1:5; Vista lateral Scale: 1:5

DESIGNED BY: João Vitor. DATE: 05/05/2026 | I | _

SIZE A3 | | | | FATEC

SCALE 1:5 | WEIGHT (kg) XXX | DRAWING NUMBER MAQUINA INTERATIVA | SHEET 1/1

This drawing is our property; it can't be reproduced or communicated without our written agreement.

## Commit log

2025-09-11 Pré-projeto
    Esse é o Pré-projeto desenvolvido para a primeira Sprint.
2025-10-02 Imagem do circuito elétrico
    Imagem do circuito elétrico criado no Frietzing criado pelo Gabriel no dia 02/10/25 - ainda necessário ajeitar o esquema eletrico
2025-10-02 Montagem do circuito no Frietzing
    PS: O Arquivo de ponte H aparenta estar meio bugado - necessário uma revisão
    [Untitled Sketch.fzz]
2025-10-07 Add files via upload
    Esta é a minuta de projeto analisada pela prof Danielle
2025-10-08 Add files via upload
    Lista de materiais atualizado com relação ao desenvolvimento até a Sprint2
    [Lista de Materiais - Sprint 2.xlsx]
